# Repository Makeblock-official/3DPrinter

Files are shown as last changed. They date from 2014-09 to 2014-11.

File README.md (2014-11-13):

[Makeblock Logo Library v2.1.0422](https://www.Makeblock.cc)

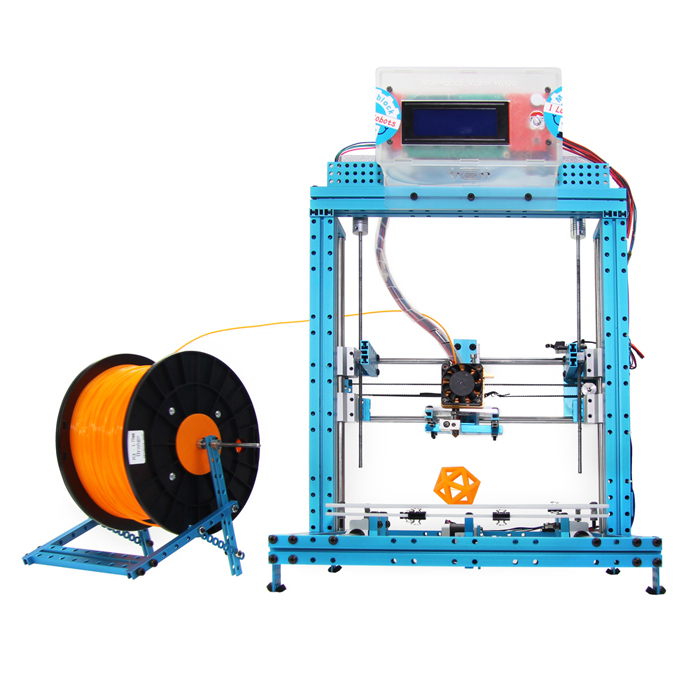
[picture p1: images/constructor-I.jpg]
Makeblock constructor
[ Makeblock Construtor I 3D printer Kit](https://www.Makeblock.cc)

The package consists of the software(Printrun-Win-Slic3r-10Mar2014),the firmware Marlin, some 3D models for testing and the structure assembly instruction.

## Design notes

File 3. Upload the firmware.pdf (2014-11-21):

# 3. Upload the firmware

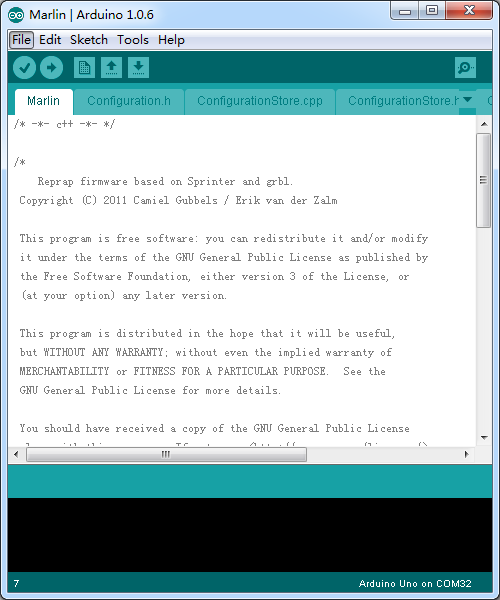
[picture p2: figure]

### Content

## 3.1 Install Arduino IDE

Please download the Arduino software from Arduino official website and install it. (Download the version according your computer system) http://arduino.cc/en/Main/Software

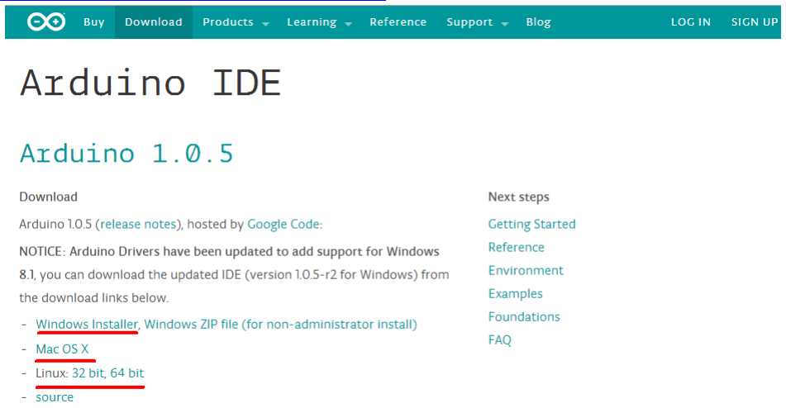
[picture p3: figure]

## 3.2 Install Arduino Drivers

You can find Arduino drivers in folder "Arduino drivers"(Both Mac and Windows).

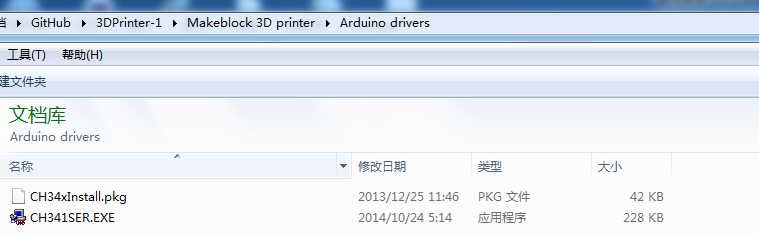
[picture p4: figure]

double click the file "CH3415SER" and click “Install” button as the below picture

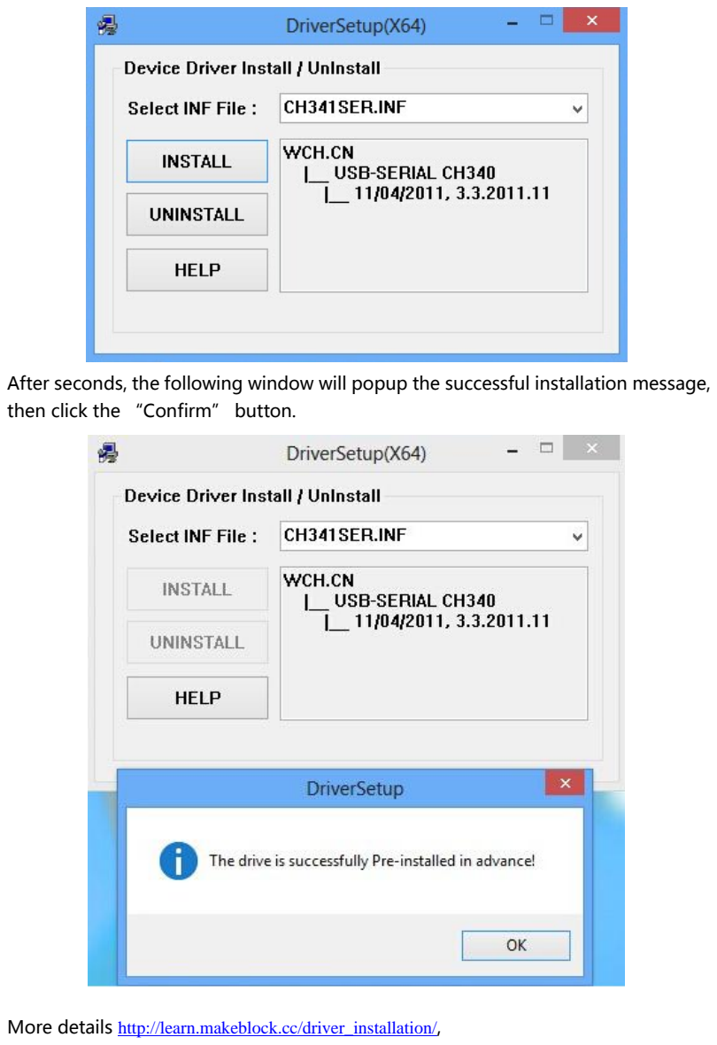
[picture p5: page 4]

After seconds, the following window will popup the successful installation message, then click the “Confirm” button.

More details http://learn.makeblock.cc/driver_installation/,

## 3.3 Open the Marlin example

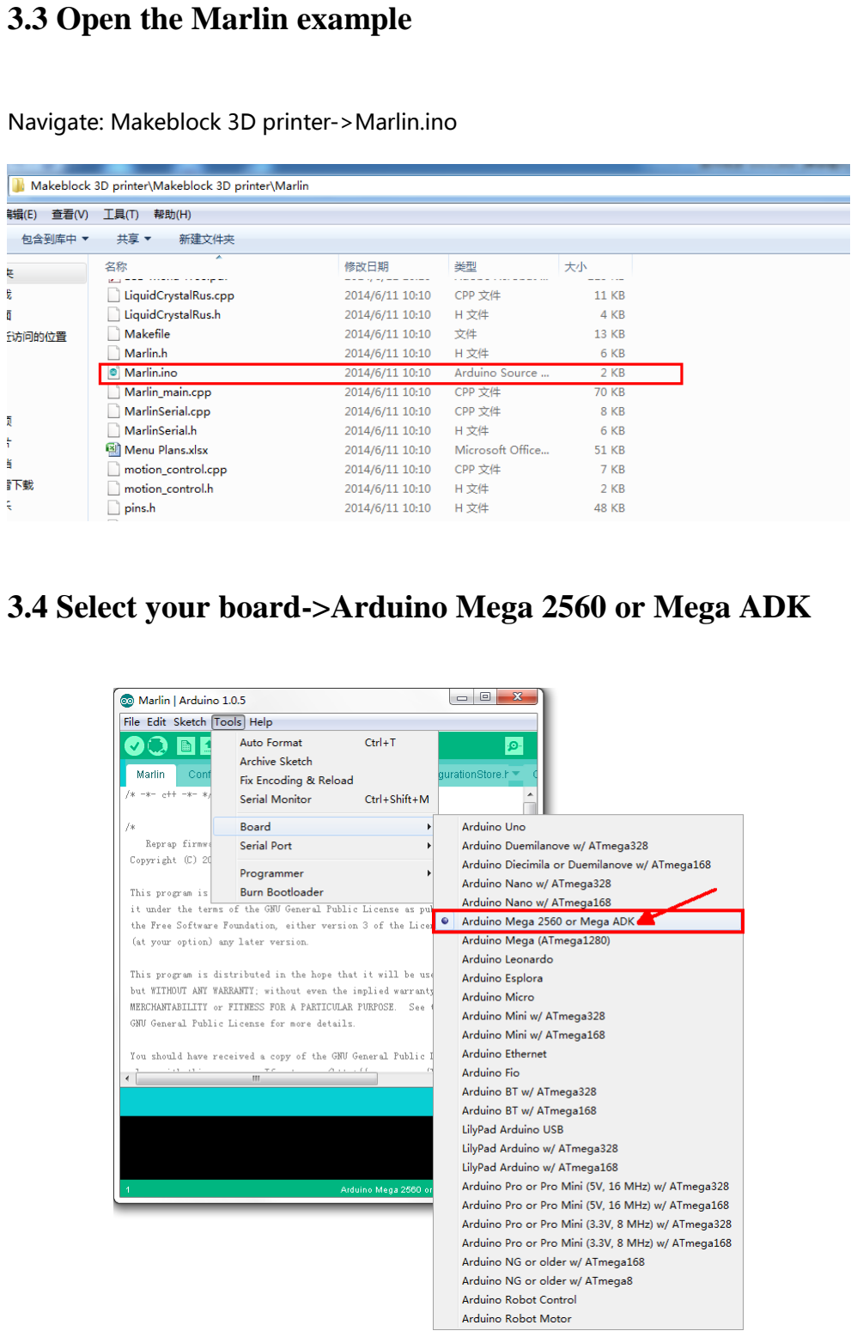
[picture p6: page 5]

Navigate: Makeblock 3D printer->Marlin.ino

## 3.4 Select your board->Arduino Mega 2560 or Mega ADK

## 3.5 Select your serial port

Select the serial device of the Arduino board from the Tools | Serial Port menu. This

is likely to be COM3 or higher (COM1and COM2 are usually reserved for hardware

serial ports). To find out, you can disconnect your Arduino board and re-open the

menu; the entry that disappears should be the Arduino board. Reconnect the board

and select that serial port.

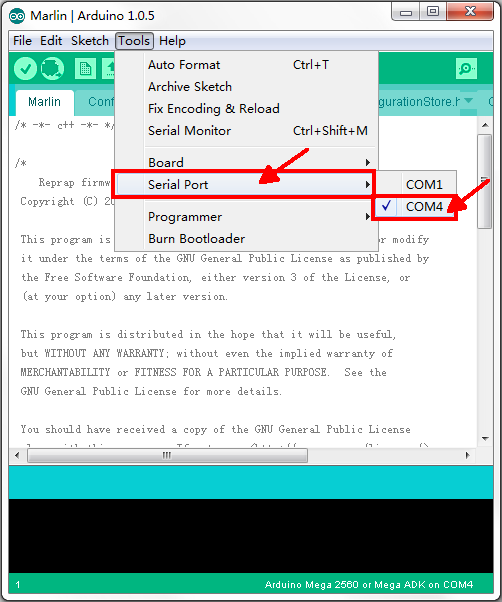
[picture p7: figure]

## 3.6 Upload the program

Now, simply click the "Upload" button in the environment. Wait a few seconds - you

should see the RX and TX leds on the board flashing. If the upload is successful, the

message "Done uploading." will appear in the status bar.

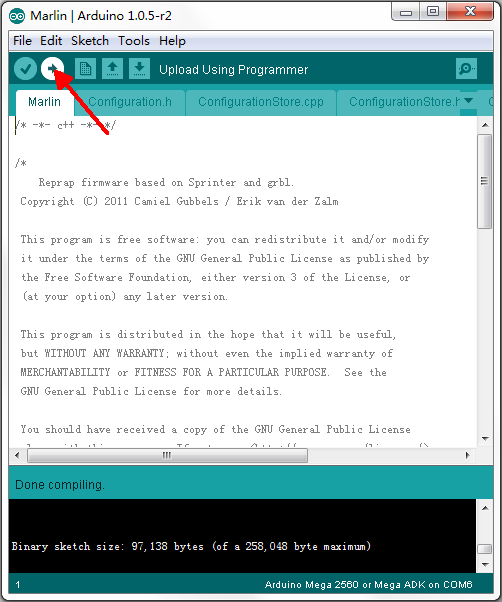
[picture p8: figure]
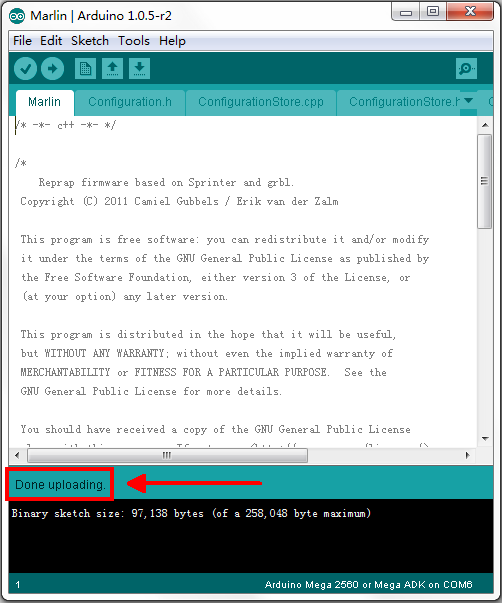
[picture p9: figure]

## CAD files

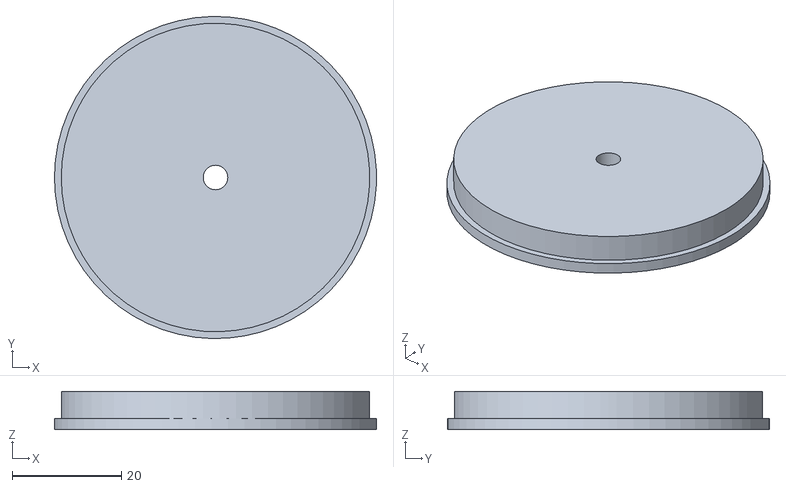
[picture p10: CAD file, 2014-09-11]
Makeblock 3D printer/3D model/Spool_D4.STL
59.0 x 59.0 x 7.00

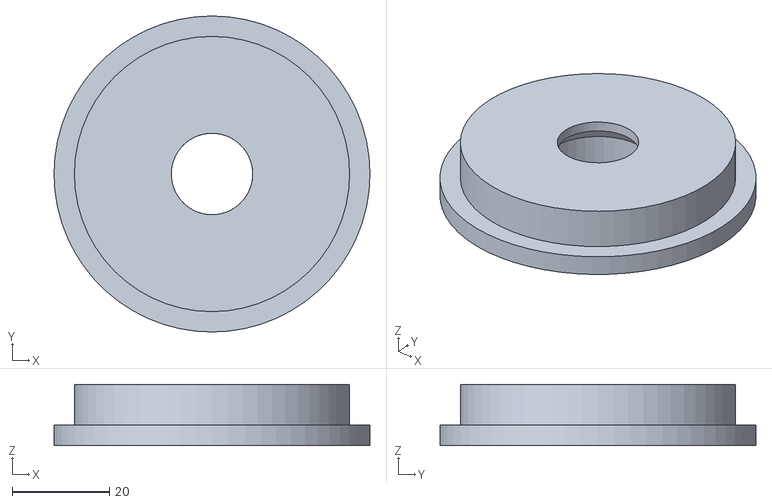
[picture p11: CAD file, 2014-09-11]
Makeblock 3D printer/3D model/Spool_608zz.STL
65.1 x 65.1 x 12.6

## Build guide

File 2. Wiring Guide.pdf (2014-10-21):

### Makeblock Constructor I 3D Printer Kit

# 2. 3D Printer Wiring Guide

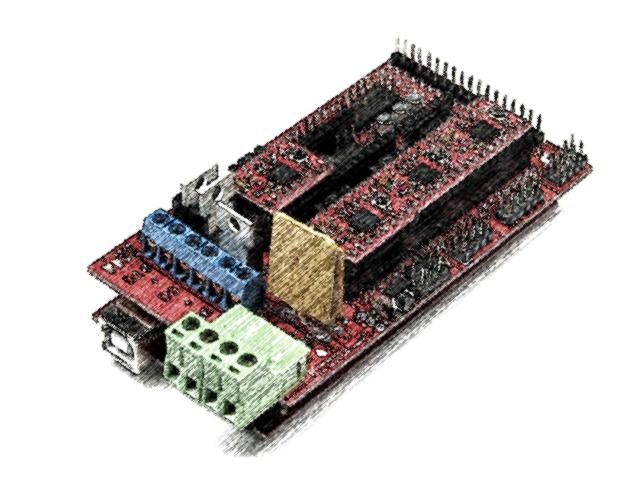
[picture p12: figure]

### Content

## 2.1. Parts Required

Parts required:

- reprap smart controller ×1
- ramps1.4 ×1
- MEGA2560 compatible board ×1
- Stepper motor driver(A4988) ×4

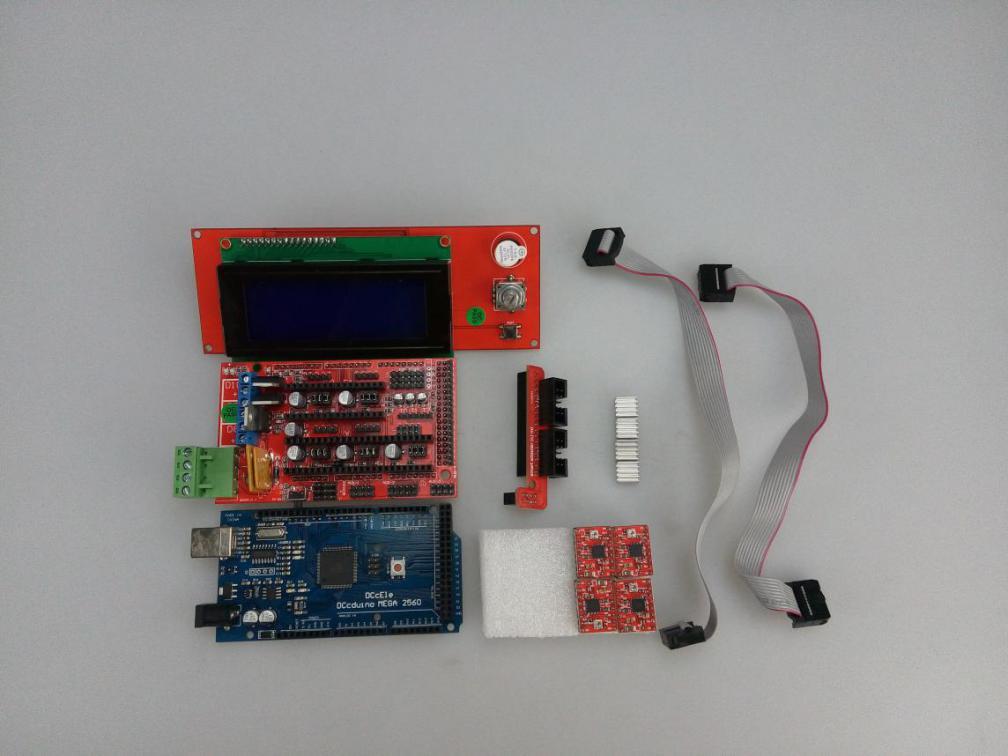
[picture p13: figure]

Mega2560 compatible board

Based on the ATmega2560 and used as the microcontroller board of our 3D printer.

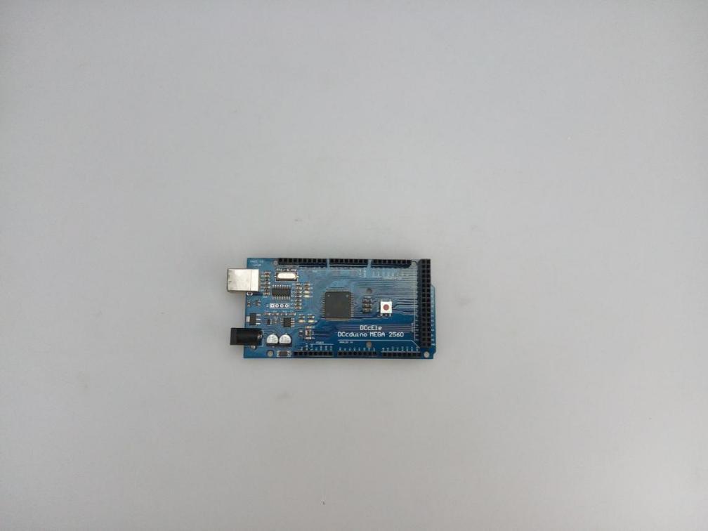
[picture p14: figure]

Ramps1.4 Shield

Ramps is short for reprap Arduino mega pololu shield, it is open source and

designed as the shield of 3D printer. For more details about this open source

hardware design can be found on the Reprap Wiki

here:http://reprap.org/wiki/RAMPS_1.4.

reprap smart controller

Used as LCD display of Constructor I 3D printer, you can easy connect it to your

Ramps using the "smart adapter". It is open source and you can know more details

from here http://reprap.org/wiki/RepRapDiscount_Smart_Controlle

Smart adapter

Stepper Motor Driver Module (A4988) Pictures are for reference only, please in

kind prevail

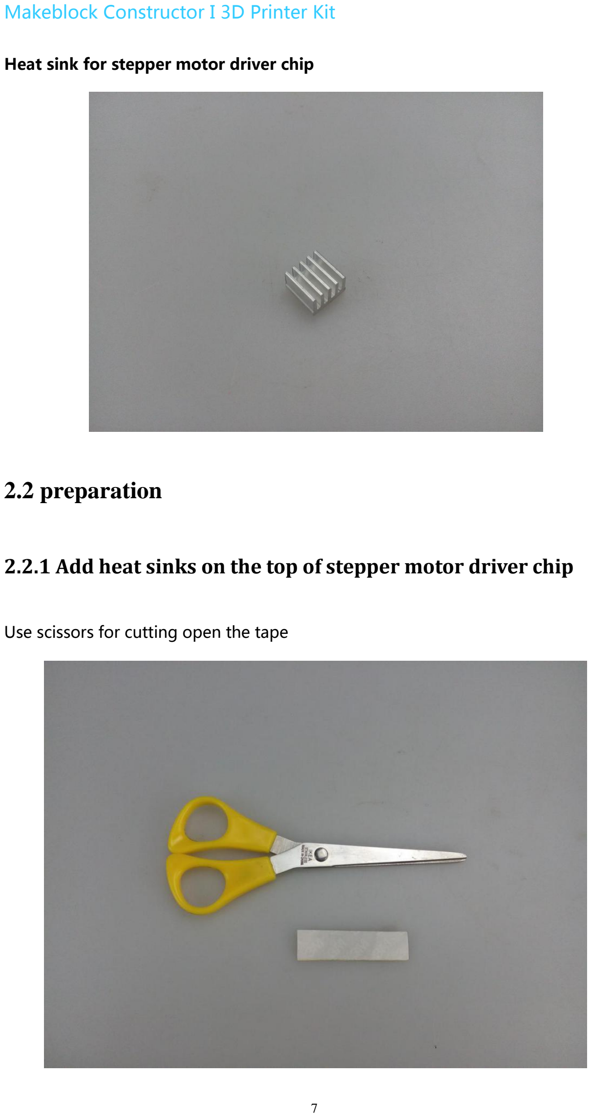
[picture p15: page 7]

Heat sink for stepper motor driver chip

## 2.2 preparation

### 2.2.1 Add heat sinks on the top of stepper motor driver chip

Use scissors for cutting open the tape

Cut the tape as the same size as heatsink

Stick the tape to the heat sink

Stick the heatsink to Chip A4988 firmly

Repeat the above step to stick other 3 modules

### 2.2.2 Plug the jumper cap into corresponding position

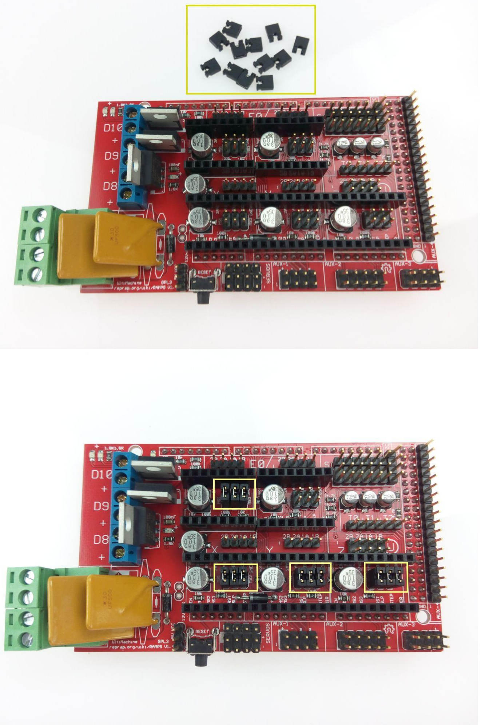
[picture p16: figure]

## 2.3 Wiring the main board part

2.3.1 Connect the stepper motor driver(A4988) to Ramp1.4.

step1. Plug in the A4988 motor driver module onto Ramp1.4 as shown below.

(ATTENTION: IF ANTI-PLUG, IT WILL SHORT-CIRCUITS.)

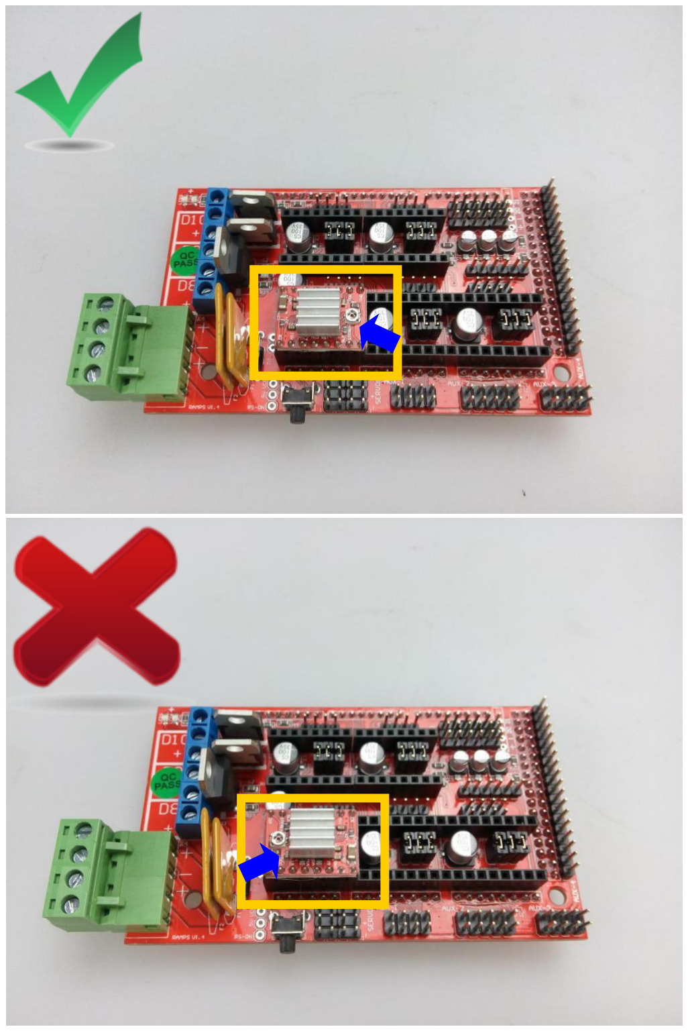
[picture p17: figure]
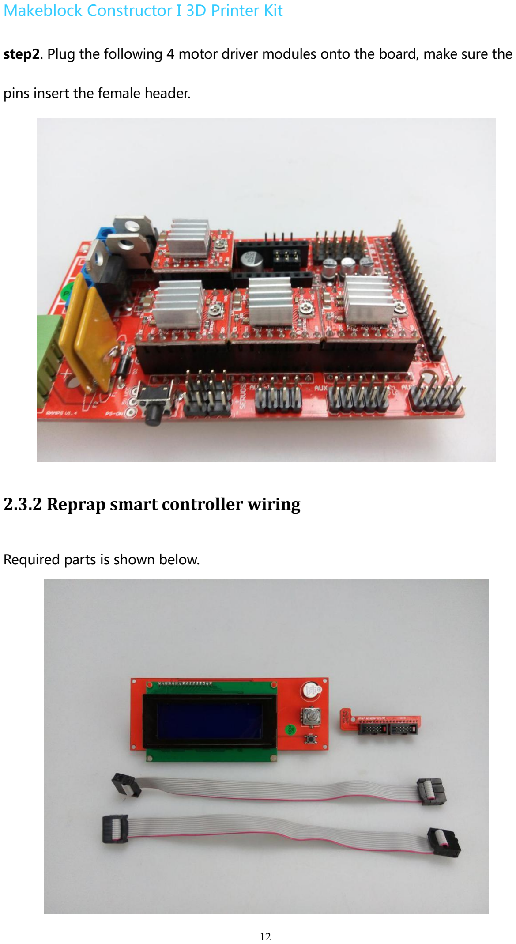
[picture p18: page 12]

step2. Plug the following 4 motor driver modules onto the board, make sure the

pins insert the female header.

### 2.3.2 Reprap smart controller wiring

Required parts is shown below.

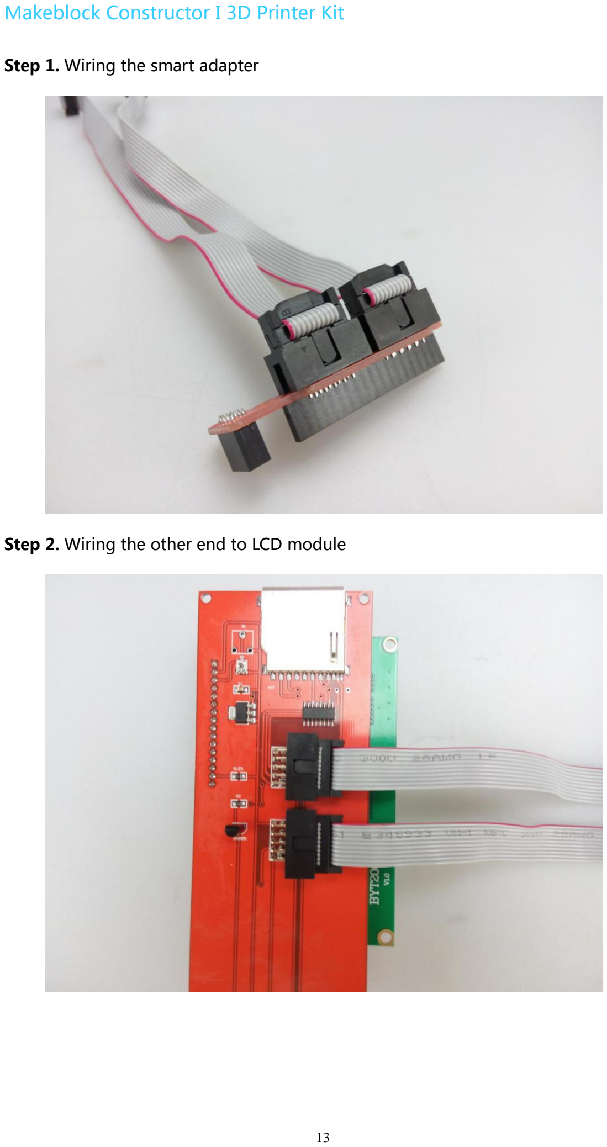
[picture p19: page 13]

Step 1. Wiring the smart adapter
Step 2. Wiring the other end to LCD module

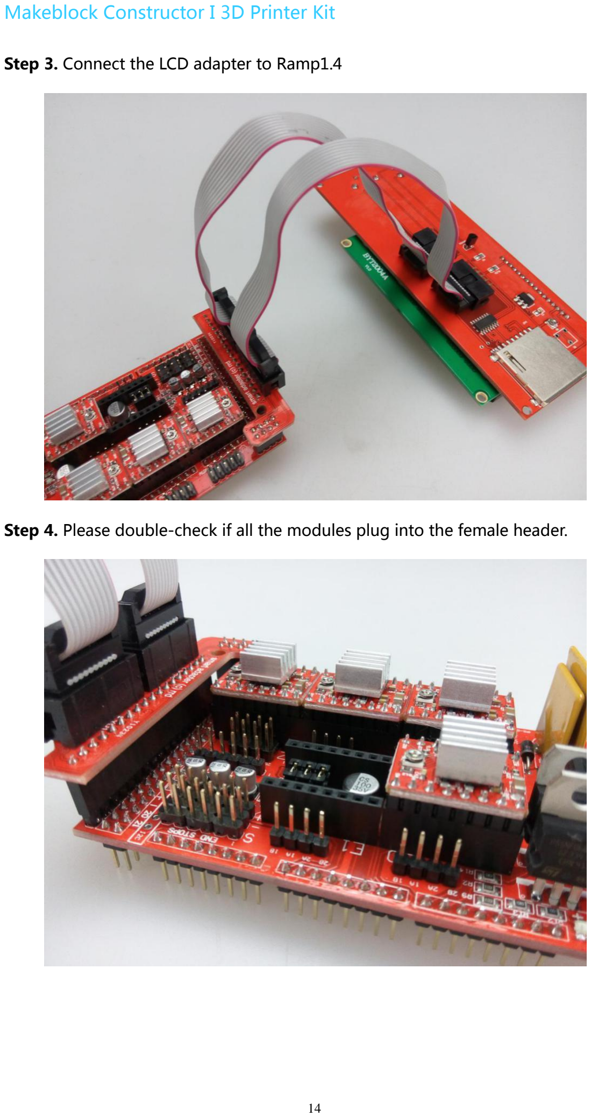
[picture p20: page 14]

Step 3. Connect the LCD adapter to Ramp1.4
Step 4. Please double-check if all the modules plug into the female header.

### 2.3.3 Connect Ramps1.4 to the main board

Step 1. Install the Ramps1.4 on the top of Mega2560 compatible board, ragged the

right side female header and plug in slowly.

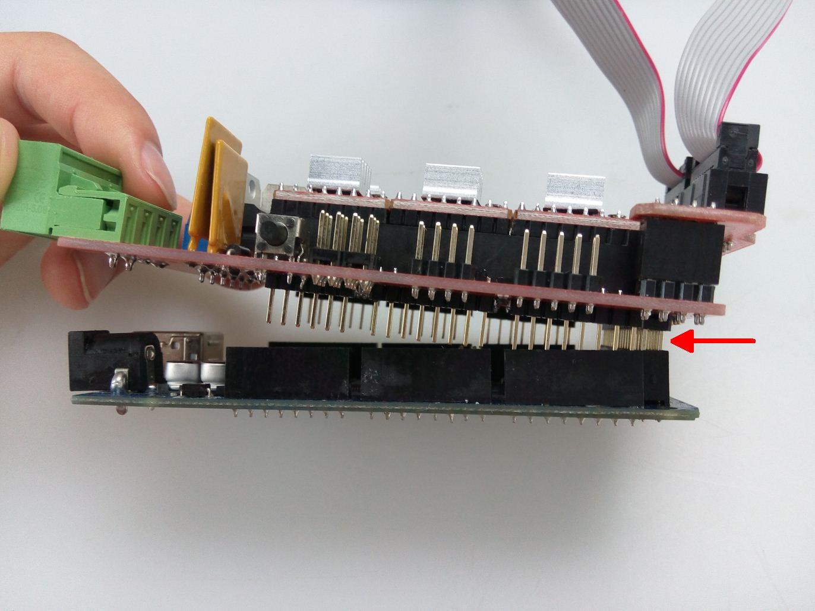
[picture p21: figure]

Step2. Double check if all the connections are right.

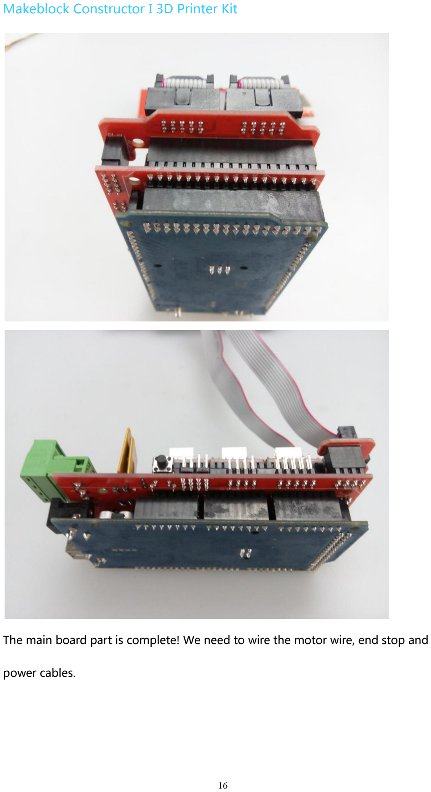
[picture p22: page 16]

The main board part is complete! We need to wire the motor wire, end stop and

power cables.

## 2.4 Wiring motors and limit switchs

Electronic wiring as show, this is RepRap original wiring figure and please follow the

actual image to wire. (Because Makeblock Constructor I 3D Printer Kit do not

contain Heated Bed, you don’t need to wire Heated Bed Power and Heated Bed

Thermistor.). Kindly advise you can pay more attention and carefully to avoid faulty

connection.

Note: Please connect the motor wiring as following order: red, blue, green and

black.

Figure out and remember the position of X/Y/Z motor and every end stop, BE

CAREFUL not to mix up the end stop.

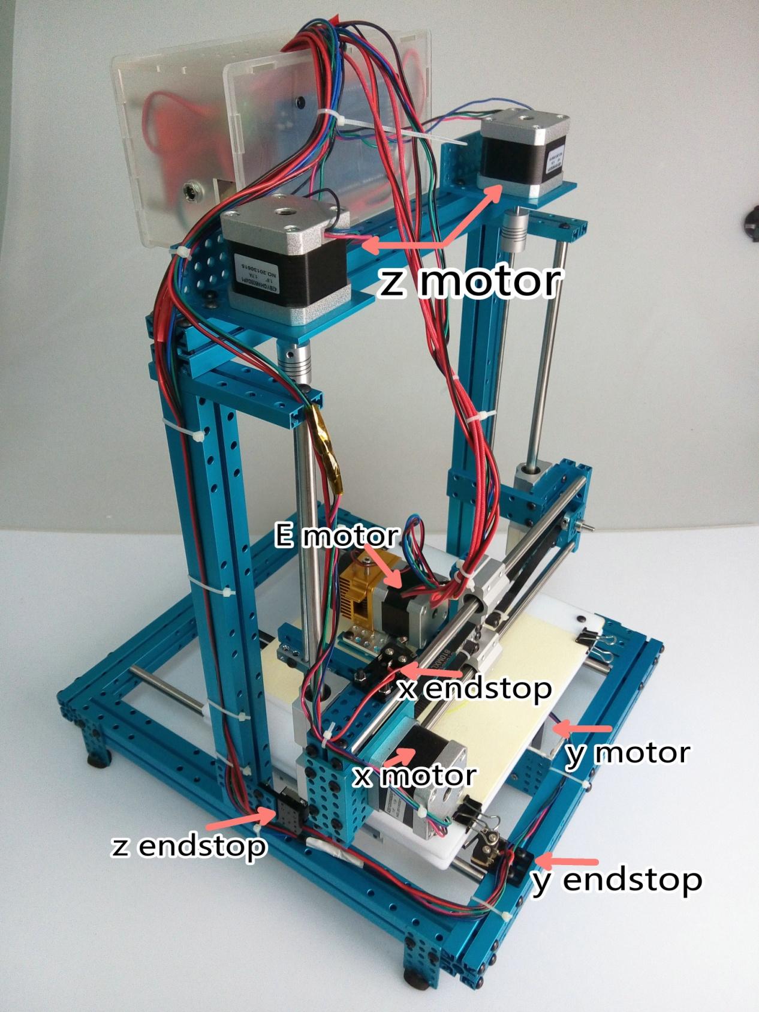
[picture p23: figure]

### 2.4.1 Wiring four stepper motors

Step1. Connect the X Motor to the connector labeled X. Ensure the Red cable is

closest to the green screw terminals on the RAMPS board (Wire orders from left to

right: red, blue, green and black).

Note: If you don't wiring by color order, the motor motion will be incorrect.

Step 2. Connect the Y Motor to the connector labeled Y. Ensure the Red cable is

closest to the green screw terminals on the RAMPS board. (Wire orders from left to right: red, blue, green and black)

Note: If you don't wiring by color order, the motor motion will be incorrect.

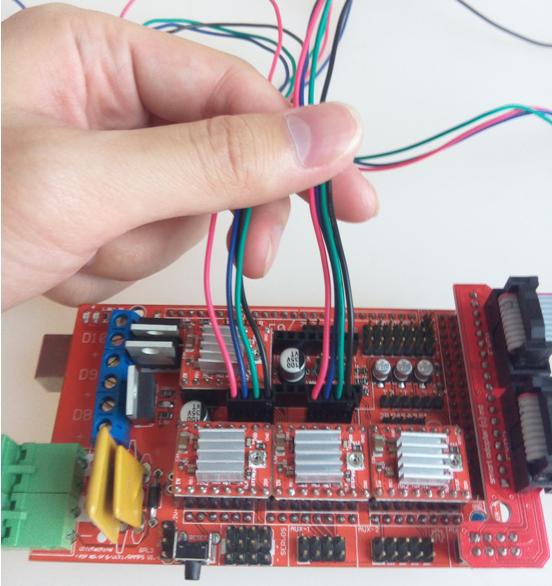
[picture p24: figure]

Step 3. Check the double-row header area around Z motor driver on the Ramp1.4

board. It can connect 2 Z motors of 3D printer.

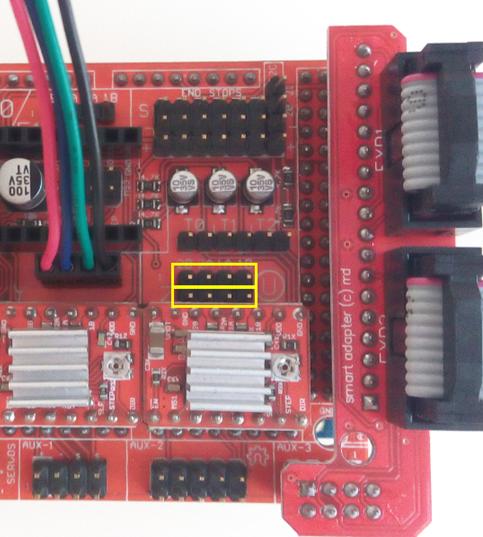
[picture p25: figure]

Step 4. Connect the two Z Motors to connectors labeled Z. Ensure the Red cable is

closest to the green screw terminals on the RAMPS board. (Wire orders from left to

right: red, blue, green and black).

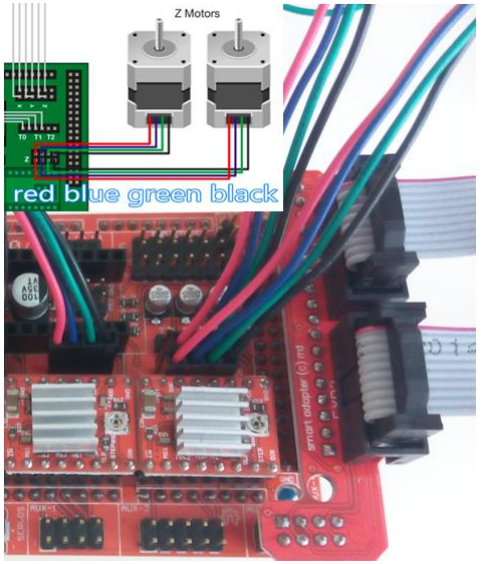
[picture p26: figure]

### 2.4.2 Wiring the extruder

Check the all components of extruder.

Step 1. Connect the Extruder Motor to the connector labeled E0. Ensure the Red

cable is closest to the green screw terminals on the RAMPS board(Wire orders from

left to right: red, blue, green and black).

Step 2. The two red wires from extruder heating pipe have no positive and negative

difference.

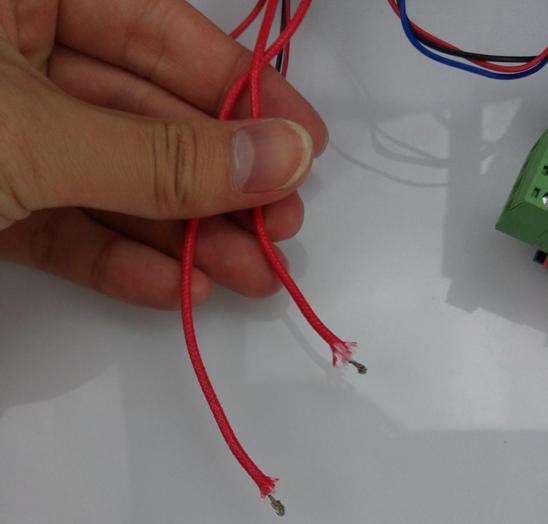
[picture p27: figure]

Connect the wire to D10, make sure the screw clamp the wire, or else the heater will

not heat up.

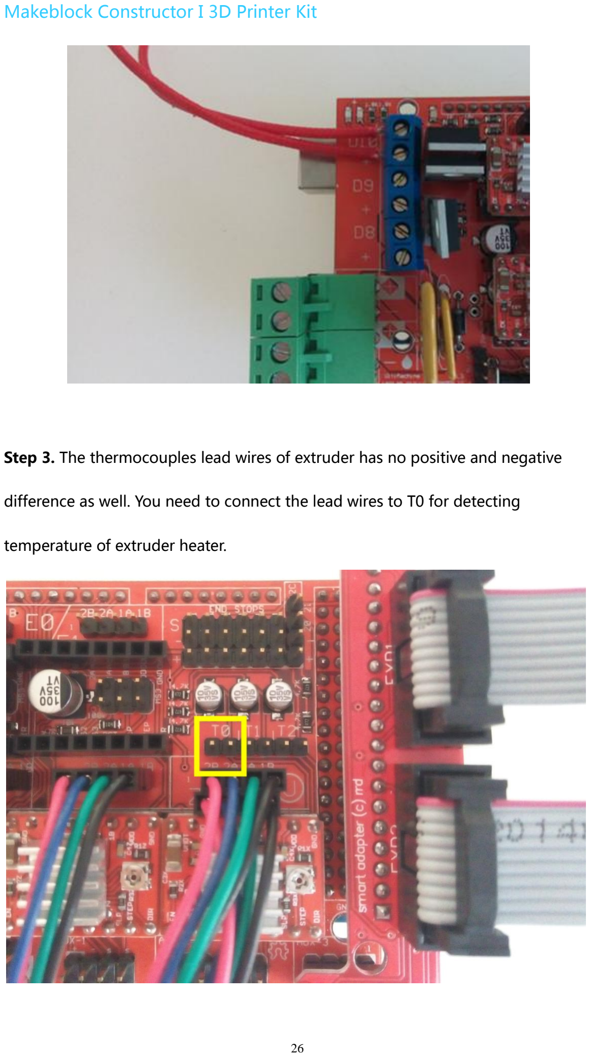
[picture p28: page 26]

Step 3. The thermocouples lead wires of extruder has no positive and negative

difference as well. You need to connect the lead wires to T0 for detecting

temperature of extruder heater.

### 2.4.3 Wring limit switches

Note: Please connect limit switchs to the male header (Area“S” and “–“).

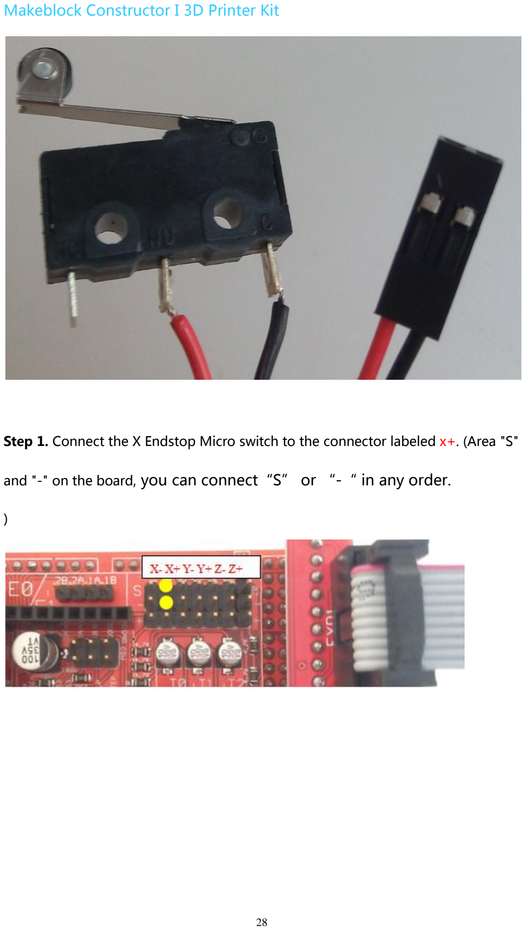
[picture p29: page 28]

Step 1. Connect the X Endstop Micro switch to the connector labeled x+. (Area "S"

and "-" on the board, you can connect“S” or “-“ in any order.

)

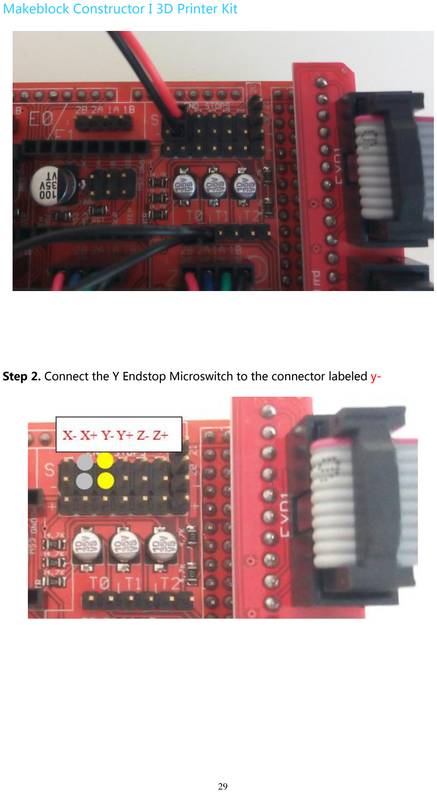
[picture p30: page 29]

Step 2. Connect the Y Endstop Microswitch to the connector labeled y-

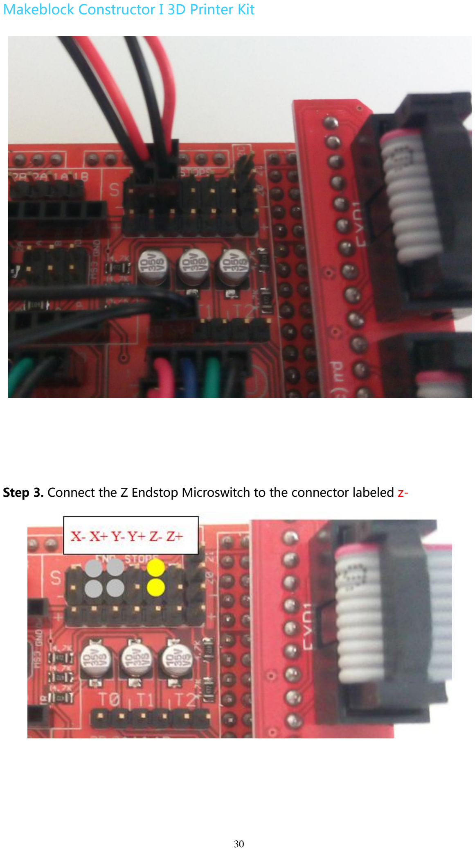
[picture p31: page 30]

Step 3. Connect the Z Endstop Microswitch to the connector labeled z-

Step 4. Please check the stop end X/Y/Z connect X+/Y-/Z- connection order

carefully. IF THE CONNECTIONS ARE INCORRECT, THE MACHINE WON’T STOP

MOVEMENT WHILE RETURN TO ZERO. If the machine won’t stop moving, please

check if the end stop connection is correct.

### 2.5 Connect power supply cables

Notice the positive and negative difference.

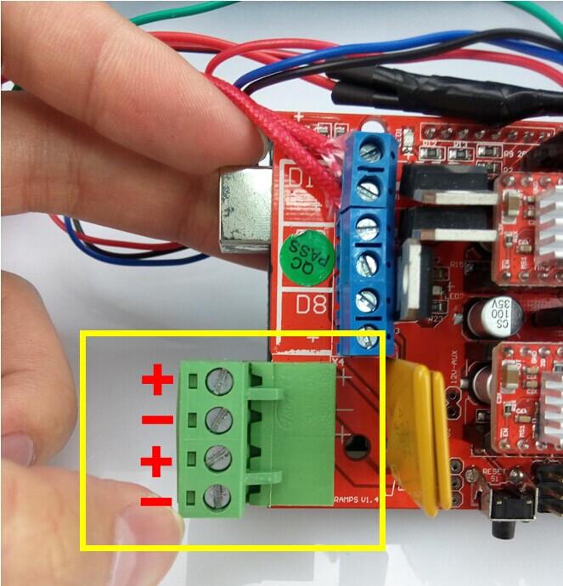
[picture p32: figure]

Step1. Connect the two wires of 12 V power supply to the corresponding position.

(The red wire is positive and the black wire is negative)

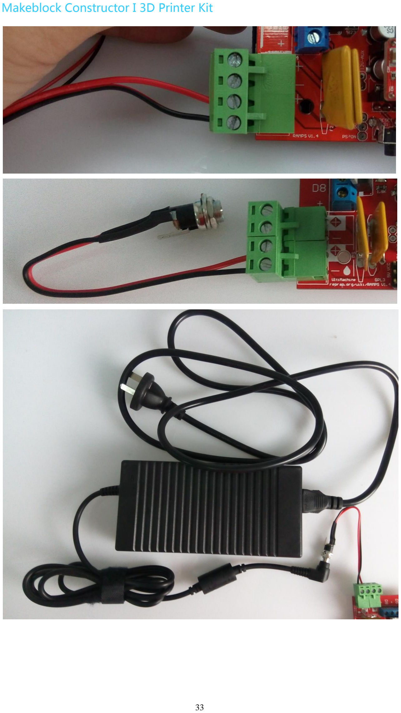
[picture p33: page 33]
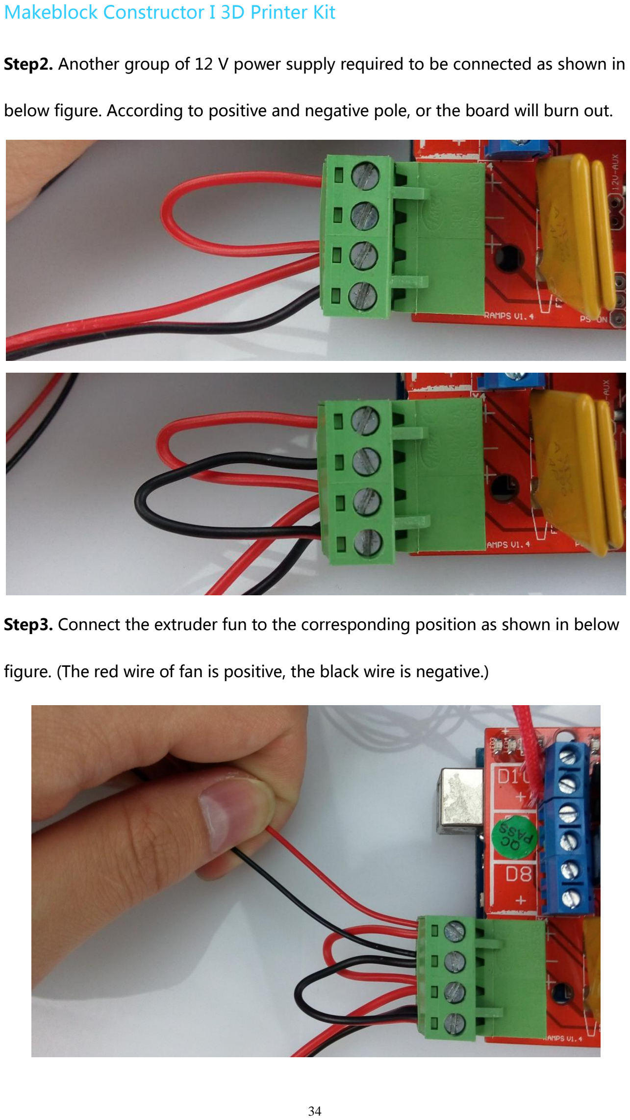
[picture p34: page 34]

Step2. Another group of 12 V power supply required to be connected as shown in

below figure. According to positive and negative pole, or the board will burn out.

Step3. Connect the extruder fun to the corresponding position as shown in below

figure. (The red wire of fan is positive, the black wire is negative.)

Step4. Please double check if you connect all the leads.

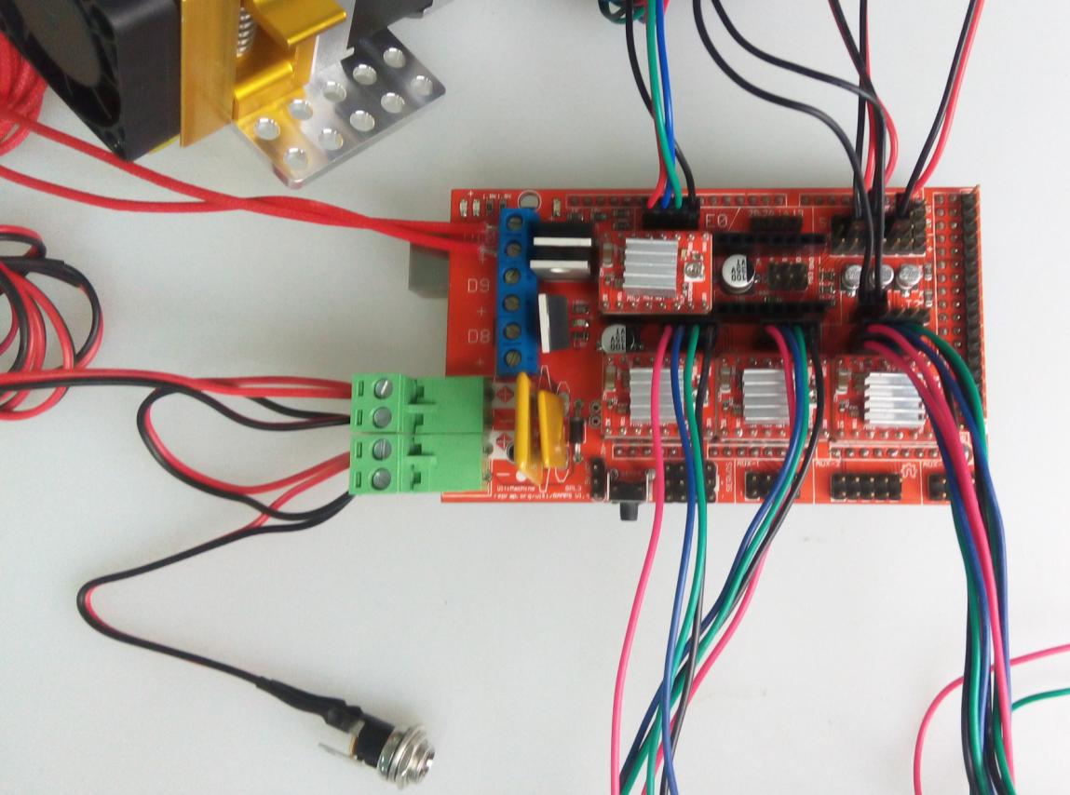
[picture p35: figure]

Please confirm as below:

If the stepper motor driver connection is correct?

If the wire connection of stepper motor order is red, blue, green and black?

If the end stop X/Y/Z connection is in correct position?

If the extruder temperature resistor is connect to T0?

If the extruder heating wire is connect to D10?

If the extruder fan connection is correct?

If the power is connection like red to positive and black to negative?

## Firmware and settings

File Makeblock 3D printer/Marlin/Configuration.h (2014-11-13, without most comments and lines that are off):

#define CONFIGURATION_H
#define STRING_VERSION_CONFIG_H __DATE__ " " __TIME__ // build date and time
#define STRING_CONFIG_H_AUTHOR "(CC, default config)" //Who made the changes.
#define SERIAL_PORT 0
#define BAUDRATE 115200
#define MOTHERBOARD 33
#define EXTRUDERS 1
#define POWER_SUPPLY 1
#define TEMP_SENSOR_0 5
#define TEMP_SENSOR_1 0
#define TEMP_SENSOR_2 0
#define TEMP_SENSOR_BED 0
#define TEMP_RESIDENCY_TIME 10  // (seconds)
#define TEMP_HYSTERESIS 3       // (degC) range of +/- temperatures considered "close" to the target one
#define TEMP_WINDOW     1       // (degC) Window around target to start the recidency timer x degC early.
#define HEATER_0_MINTEMP 5
#define HEATER_1_MINTEMP 5
#define HEATER_2_MINTEMP 5
#define BED_MINTEMP 5
#define HEATER_0_MAXTEMP 260
#define HEATER_1_MAXTEMP 260
#define HEATER_2_MAXTEMP 260
#define BED_MAXTEMP 150
#define BANG_MAX 256 // limits current to nozzle while in bang-bang mode; 256=full current
#define PID_MAX 256 // limits current to nozzle while PID is active (see PID_FUNCTIONAL_RANGE below); 256=full current
#define MAX_BED_POWER 256 // limits duty cycle to bed; 256=full current
#define PREVENT_DANGEROUS_EXTRUDE
#define PREVENT_LENGTHY_EXTRUDE
#define EXTRUDE_MINTEMP 170
#define EXTRUDE_MAXLENGTH (X_MAX_LENGTH+Y_MAX_LENGTH) //prevent extrusion of very large distances.
#define ENDSTOPPULLUPS // Comment this out (using // at the start of the line) to disable the endstop pullup resistors
  #define ENDSTOPPULLUP_XMAX
  #define ENDSTOPPULLUP_YMAX
  #define ENDSTOPPULLUP_ZMAX
  #define ENDSTOPPULLUP_XMIN
  #define ENDSTOPPULLUP_YMIN
  #define ENDSTOPPULLUP_ZMIN
const bool X_ENDSTOPS_INVERTING = true; // set to true to invert the logic of the endstops.
const bool Y_ENDSTOPS_INVERTING = true; // set to true to invert the logic of the endstops.
const bool Z_ENDSTOPS_INVERTING = true; // set to true to invert the logic of the endstops.
#define X_ENABLE_ON 0
#define Y_ENABLE_ON 0
#define Z_ENABLE_ON 0
#define E_ENABLE_ON 0 // For all extruders
#define DISABLE_X false
#define DISABLE_Y false
#define DISABLE_Z false
#define DISABLE_E false // For all extruders
#define INVERT_X_DIR true    // for Mendel set to false, for Orca set to true
#define INVERT_Y_DIR false    // for Mendel set to true, for Orca set to false
#define INVERT_Z_DIR true     // for Mendel set to false, for Orca set to true
#define INVERT_E0_DIR true   // for direct drive extruder v9 set to true, for geared extruder set to false
#define INVERT_E1_DIR false    // for direct drive extruder v9 set to true, for geared extruder set to false
#define INVERT_E2_DIR false   // for direct drive extruder v9 set to true, for geared extruder set to false
#define X_HOME_DIR 1
#define Y_HOME_DIR -1
#define Z_HOME_DIR -1
#define min_software_endstops true //If true, axis won't move to coordinates less than HOME_POS.
#define max_software_endstops true  //If true, axis won't move to coordinates greater than the defined lengths below.
#define X_MAX_POS 125
#define X_MIN_POS 0
#define Y_MAX_POS 160
#define Y_MIN_POS 0
#define Z_MAX_POS 140
#define Z_MIN_POS 0
#define X_MAX_LENGTH (X_MAX_POS - X_MIN_POS)
#define Y_MAX_LENGTH (Y_MAX_POS - Y_MIN_POS)
#define Z_MAX_LENGTH (Z_MAX_POS - Z_MIN_POS)
#define MANUAL_X_HOME_POS 0
#define MANUAL_Y_HOME_POS 0
#define MANUAL_Z_HOME_POS 0
#define NUM_AXIS 4 // The axis order in all axis related arrays is X, Y, Z, E
#define HOMING_FEEDRATE {50*60, 50*60, 2.5*60, 0}  // set the homing speeds (mm/min)
#define DEFAULT_AXIS_STEPS_PER_UNIT   {87.58,87.58,(200.0*16/0.7), 92.65}  // default steps per unit for ultimaker
#define DEFAULT_MAX_FEEDRATE          {500, 500, 2, 45}    // (mm/sec)
#define DEFAULT_MAX_ACCELERATION      {9000,9000,100,300}    // X, Y, Z, E maximum start speed for accelerated moves. E default values are good for skeinforge 40+, for older versions raise them a lot.
#define DEFAULT_ACCELERATION          2000    // X, Y, Z and E max acceleration in mm/s^2 for printing moves
#define DEFAULT_RETRACT_ACCELERATION  300   // X, Y, Z and E max acceleration in mm/s^2 for r retracts
#define DEFAULT_XYJERK                20.0    // (mm/sec)
#define DEFAULT_ZJERK                 0.4     // (mm/sec)
#define DEFAULT_EJERK                 2.0    // (mm/sec)
#define PLA_PREHEAT_HOTEND_TEMP 200
#define PLA_PREHEAT_HPB_TEMP 70
#define PLA_PREHEAT_FAN_SPEED 255   // Insert Value between 0 and 255
#define ABS_PREHEAT_HOTEND_TEMP 230
#define ABS_PREHEAT_HPB_TEMP 100
#define ABS_PREHEAT_FAN_SPEED 255   // Insert Value between 0 and 255
#define REPRAP_DISCOUNT_SMART_CONTROLLER
 #define ULTIPANEL
 #define NEWPANEL
  #define SDSUPPORT
  #define ULTRA_LCD
    #define LCD_WIDTH 20
    #define LCD_HEIGHT 4
#include "Configuration_adv.h"
#include "thermistortables.h"

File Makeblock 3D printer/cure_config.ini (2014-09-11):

[profile]
layer_height = 0.21
wall_thickness = 0.8
retraction_enable = True
solid_layer_thickness = 1
fill_density = 10
nozzle_size = 0.4
print_speed = 45
print_temperature = 205
print_temperature2 = 0
print_temperature3 = 0
print_temperature4 = 0
print_bed_temperature = 0
support = None
platform_adhesion = None
support_dual_extrusion = Both
wipe_tower = False
wipe_tower_volume = 15
ooze_shield = False
filament_diameter = 1.75
filament_diameter2 = 0
filament_diameter3 = 0
filament_diameter4 = 0
filament_flow = 95
retraction_speed = 60
retraction_amount = 6
retraction_dual_amount = 16.5
retraction_min_travel = 1.5
retraction_combing = True
retraction_minimal_extrusion = 0.02
retraction_hop = 0.0
bottom_thickness = 0.3
layer0_width_factor = 100
object_sink = 0.0
overlap_dual = 0.15
travel_speed = 80
bottom_layer_speed = 20
infill_speed = 0.0
inset0_speed = 20
insetx_speed = 45
cool_min_layer_time = 5
fan_enabled = True
skirt_line_count = 1
skirt_gap = 3.0
skirt_minimal_length = 150.0
fan_full_height = 0.5
fan_speed = 100
fan_speed_max = 100
cool_min_feedrate = 10
cool_head_lift = False
solid_top = True
solid_bottom = True
fill_overlap = 15
support_type = Grid
support_angle = 60
support_fill_rate = 15
support_xy_distance = 0.7
support_z_distance = 0.15
spiralize = False
simple_mode = False
brim_line_count = 20
raft_margin = 5
raft_line_spacing = 1.0
raft_base_thickness = 0.3
raft_base_linewidth = 0.7
raft_interface_thickness = 0.2
raft_interface_linewidth = 0.2
raft_airgap = 0.22
raft_surface_layers = 2
fix_horrible_union_all_type_a = True
fix_horrible_union_all_type_b = False
fix_horrible_use_open_bits = False
fix_horrible_extensive_stitching = False
plugin_config = 
object_center_x = -1
object_center_y = -1

[alterations]
start.gcode = ;Sliced at: {day} {date} {time}
	;Basic settings: Layer height: {layer_height} Walls: {wall_thickness} Fill: {fill_density}
	;Print time: {print_time}
	;Filament used: {filament_amount}m {filament_weight}g
	;Filament cost: {filament_cost}
	;M190 S{print_bed_temperature} ;Uncomment to add your own bed temperature line
	;M109 S{print_temperature} ;Uncomment to add your own temperature line
	G21        ;metric values
	G90        ;absolute positioning
	M82        ;set extruder to absolute mode
	M107       ;start with the fan off
	G28 X0 Y0  ;move X/Y to min endstops
	G28 Z0     ;move Z to min endstops
	G1 Z15.0 F{travel_speed} ;move the platform down 15mm
	G92 E0                  ;zero the extruded length
	G1 F200 E3              ;extrude 3mm of feed stock
	G92 E0                  ;zero the extruded length again
	G1 F{travel_speed}
	;Put printing message on LCD screen
	M117 Printing...
end.gcode = ;End GCode
	M104 S0                     ;extruder heater off
	M140 S0                     ;heated bed heater off (if you have it)
	G91                                    ;relative positioning
	G1 E-1 F300                            ;retract the filament a bit before lifting the nozzle, to release some of the pressure
	G1 Z+0.5 E-5 X-20 Y-20 F{travel_speed} ;move Z up a bit and retract filament even more
	G28 X0 Y0                              ;move X/Y to min endstops, so the head is out of the way
	M84                         ;steppers off
	G90                         ;absolute positioning
start2.gcode = ;Sliced at: {day} {date} {time}
	;Basic settings: Layer height: {layer_height} Walls: {wall_thickness} Fill: {fill_density}
	;Print time: {print_time}
	;Filament used: {filament_amount}m {filament_weight}g
	;Filament cost: {filament_cost}
	;M190 S{print_bed_temperature} ;Uncomment to add your own bed temperature line
	;M104 S{print_temperature} ;Uncomment to add your own temperature line
	;M109 T1 S{print_temperature2} ;Uncomment to add your own temperature line
	;M109 T0 S{print_temperature} ;Uncomment to add your own temperature line
	G21        ;metric values
	G90        ;absolute positioning
	M107       ;start with the fan off
	G28 X0 Y0  ;move X/Y to min endstops
	G28 Z0     ;move Z to min endstops
	G1 Z15.0 F{travel_speed} ;move the platform down 15mm
	T1                      ;Switch to the 2nd extruder
	G92 E0                  ;zero the extruded length
	G1 F200 E10             ;extrude 10mm of feed stock
	G92 E0                  ;zero the extruded length again
	G1 F200 E-{retraction_dual_amount}
	T0                      ;Switch to the first extruder
	G92 E0                  ;zero the extruded length
	G1 F200 E10             ;extrude 10mm of feed stock
	G92 E0                  ;zero the extruded length again
	G1 F{travel_speed}
	;Put printing message on LCD screen
	M117 Printing...
end2.gcode = ;End GCode
	M104 T0 S0                     ;extruder heater off
	M104 T1 S0                     ;extruder heater off
	M140 S0                     ;heated bed heater off (if you have it)
	G91                                    ;relative positioning
	G1 E-1 F300                            ;retract the filament a bit before lifting the nozzle, to release some of the pressure
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

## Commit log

2014-09-11 First Upload
    [Configuration.h, Configuration_adv.h, Menu Plans.xlsx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]
2014-10-29 Update some parameters in Marlin
    [Configuration.h, Spool_D4.STL, test box.STL]
2014-11-13 update some other parameters in Marlin
    [Configuration.h, Spool_D4.STL, test box.STL]
2014-11-20 Update document and add mac arduino drivers
2014-12-17 240->160
    exchange the 240 D4 with 160mm D4
2015-03-05 update the document 2. wiring guide
    update the document 2. wiring guide. Content about change the wires'
    color of power plug
